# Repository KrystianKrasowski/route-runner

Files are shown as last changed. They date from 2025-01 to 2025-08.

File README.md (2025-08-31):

# Route Runner

## Table of contents

- [Overview](#overview)
- [Usage](#usage)
    - [Command referene](#command-reference)
    - [Dualshock 2 command mapping](#command---dualshock2-mapping)
    - [Modes reference](#modes-reference)
    - [LED modes mapping](#modes---led-indicator-mapping)
- [Hardware](#hardware)
    - [Power supply](#power-supply)
    - [GPIO usage summary](#gpio-usage-summary)
    - [Other peripherals usage summary](#other-peripheral-usage-summary)
    - [Electrical schematics](#electrical-schematics)
- [Software](#software)
    - [Application architecture](#application-architecture)
- [Development](#development)
- [Future work](#future-work)
- [Decision log](#decision-log)

## Overview

[YouTube video](https://youtu.be/DjguqcQfWMA)

Route runner is a name of the line following robot project. It is built using the following components:
* STM32 NUCLEO-F303 board as a microcontroller
* 2 DC motors driven by simple L293D driver
* Pololu's QTR-HD-06A line sensor
* Dualshock2 remote control
* 1 mode indicator LED
* Two LM2596 step-down voltage converters with the following settings:
    * 7V for the motors
    * 5V for the MCU and L293D logic

For the power details visit the [Power supply](#power-supply) section

## Usage
* Turn on the device using ON/OFF switch. Mode indicator displays MANUAL CONTROL mode.
* Place the vehicle or simply run it on the black line. Mode indicator displays DETECTED state. 
* Start line following by issuing FOLLOW command. Mode indicator displays TRACKING state.

### Command reference
* FORWARD - move forward
* BACKWARD - move backward
* RIGHT - turn right
* LEFT - turn left
* FOLLOW - start tracking the route
* BREAK - stop stracking
* PID Tune, Kp up/down - increase/decrease propotional factor by 10
* PID Tune, Ki up/down - increase/decrease integral factor by 1
* PID Tune, Kd up/down - increase/decrease derivative factor by 100

### Command - dualshock2 mapping
* FORWARD - R2
* BACKWARD - L2
* RIGHT - R2 or L2 + RIGHT
* LEFT - R2 or L2 + LEFT
* FOLLOW - START
* BREAK - CROSS
* PID Tune, Kp up - SQUARE + R1
* PID Tune, Kp down - SQUARE + L1
* PID Tune, Ki up - TRIANGLE + R1
* PID Tune, Ki down - TRIANGLE + L1
* PID Tune, Kd up - CIRCLE + R1
* PID Tune, Kd down - CIRCLE + L1

### Modes reference
* MANUAL - vehicle can be manually controlled
* DETECTED - vehicle sees the route beneath
* TRACKING - either FOLLOWING or RECOVERING
* FOLLOWING - vehicle sees and follows the route
* RECOVERING - vehicle does not see but still tries to get back on the route

> Note that the RECOVERING mode lasts only for 500ms unless route runner gets back on the route. After that time the vehicle will stop tracking.

### Modes - LED indicator mapping
* MANUAL - 1 short blink per second
* DETECTED - 2 short blinks per second
* TRACKING - 4 short blinks per second
* STACK OVERFLOW (FreeRTOS) 1 short blink, 1 long blink

> Short blink is a sequence `on -> off` with 250ms duration

> Long blink is a sequence `on -> off` with 500ms duration

## Hardware
* The line sensor is positioned at 4mm above the surface and the calibration is hardcoded.

### Power supply
The device is powered by two 18650 Li-ion 2500mAh 20A baterries of total voltage equal to 7.4V (3.7V each). The power buses are distributed as follows:
* 7V power bus provided by one of the LM2596 voltage converter. Used by L293D for DC motor inputs. Note that due to quite high voltage drops on L293D the effective voltage for DC motors whould oscilate around ~5V. This is not impressive and is the area to improve in the further project iterations.
* 5V power bus provided by the second LM2596 voltage converter. Used by L293D logic and the MCU
* 3.3V power bus provided by MCU. Used by the Dualshock2 receiver and state indicator
* 3.3V analog power bus provided by MCU. Used by line sensor
* Common GND bus for all components

### GPIO usage summary
* Motion:
    * **PB0** (D3) - PWM (tim3, ch3) for left motor
    * PB6 (D5) - A1 for right motor
    * PB7 (D4) - A2 for right motor
    * **PB1** (D6) - PWM (tim3, ch4) for right motor
    * PA10 (D0) - A2 for left motor
    * PA12 (D2) - A1 for left motor
* Remote control:
    * **PB5** (D11) - MOSI
    * **PB4** (D12) - MISO
    * **PB3** (D13) - SCK
    * PF0 (D7) - CS
* Line sensing:
    * *PA1* (A1) - channel 1
    * *PA3* (A2) - channel 2
    * *PA4* (A3) - channel 3
    * *PA5* (A4) - channel 4
    * *PA6* (A5) - channel 5
    * *PA7* (A6) - channel 6
* Status indicator
    * **PA8** (D9)
* USART
    * *PA15* - USART Rx
    * *PA2* - USART Tx

### Other peripheral usage summary
* TIM2 - timer for (dualshock2) MANUAL CONTROL communication trigger
* TIM3 channel 4 - timer for PWM signal for left motor (PB1)
* TIM3 channel 3 - timer for PWM signal for right motor (PB0)
* TIM6 - timer trigger for ADC conversion by TRGO, every 1ms
* TIM7 - timer for toggle sequence for blinking LED status indicator
* TIM15 - off route guard
* ADC12 in dual mode with DMA controller for conversions readings
* SPI1 bus - communication with Dualshock2 controller (via DMA)
* USART2 - serial communication with PC

Pins in **bold** are unchangeable. *Italic* pin change may implicate other changes.

### Electrical schematics
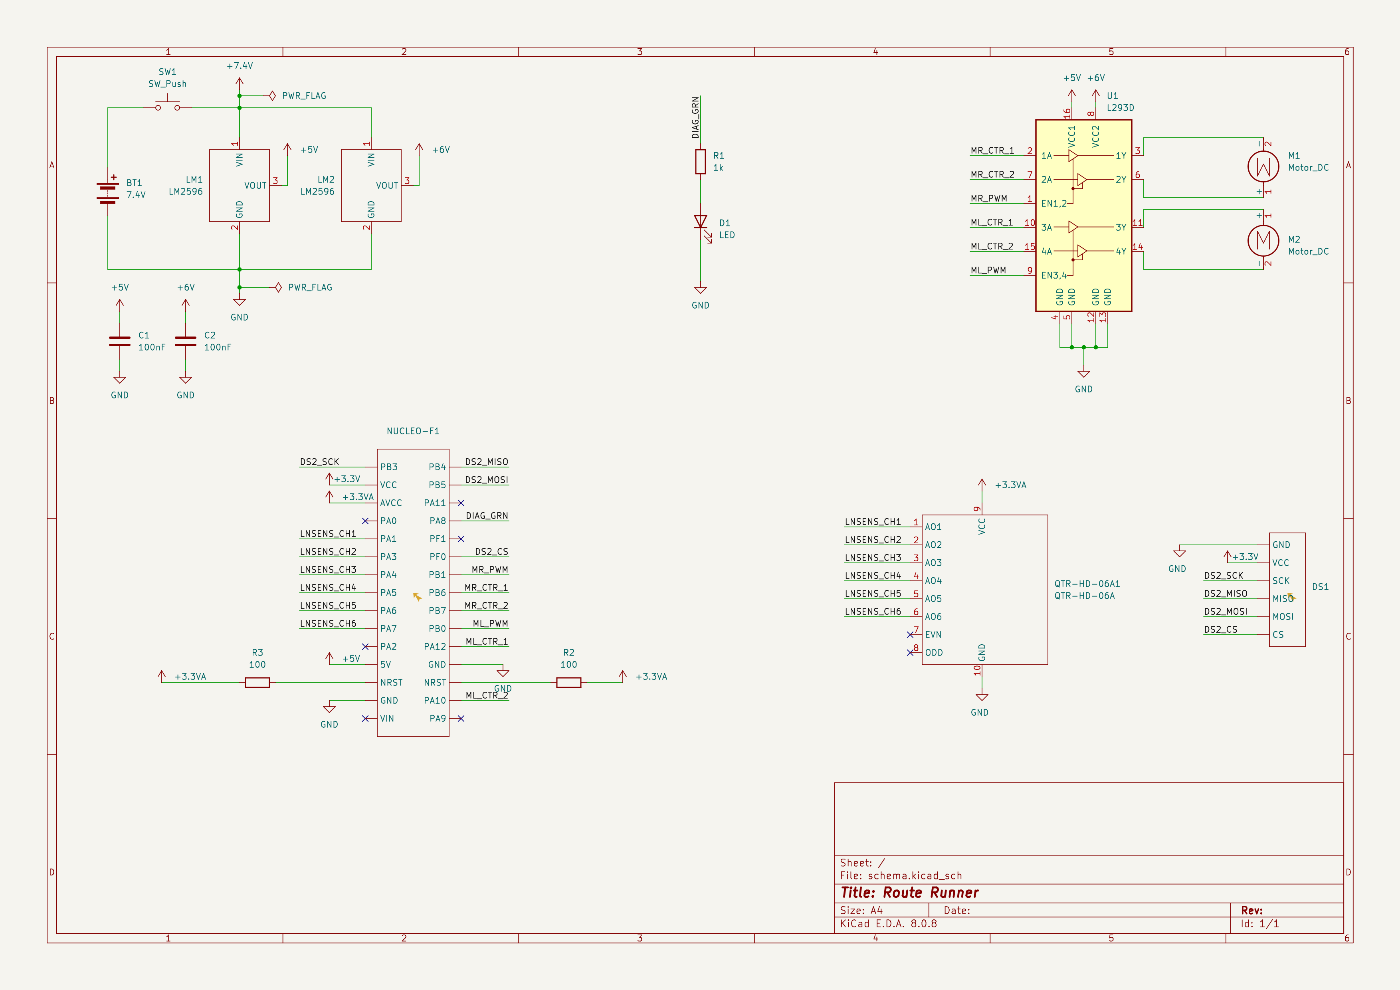
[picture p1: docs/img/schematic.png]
schematic


## Software

### Application architecture

Software architecture is inspired by the hexagonal (ports and adapters) pattern. The main goal of this approach was to be abe to embed the domain into any other MCU platform, wherher to use RTOS or bare metal, with or without STM32 HAL, etc. Any infrastructure change must not imply the domain logic changes.

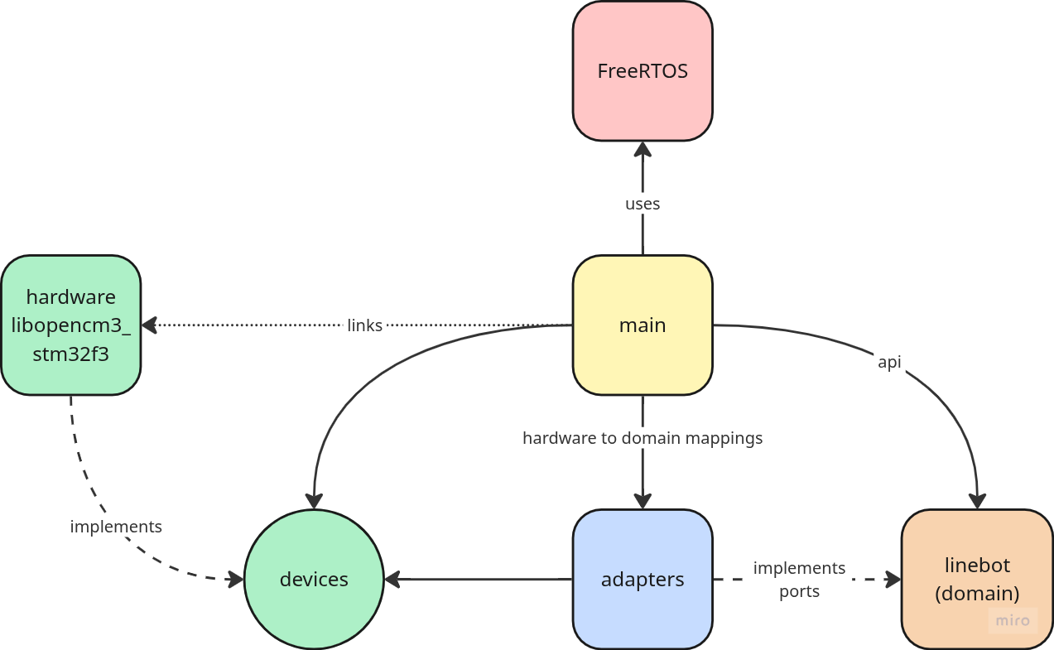
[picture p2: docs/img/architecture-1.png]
lib-dependency


## Development

Requirements:
* arm-none-eabi toolchain
* cmake

```bash
# build for flash
cmake --preset <release | debug>
cmake --build --preset <release | debug>

# flash
cmake --build --preset <release | debug> --target flash

# build for test
cmake --preset test
cmake --build --preset test
ctest --preset test
```

### Vim + LSP (clangd) setup

In order to work with vim+lsp driven by clangd keep in mind that the clangd must be run with `--query-driver` argument.
Here is an example of clangd lsp configuration via the vim-lsp-settings plugin

```
// PROJECT_ROOT/.vim-lsp-settings/settings.json
{
    "clangd": {
        "args": ["--query-driver=/usr/bin/arm-none-eabi-*"]
    }
}
```

## Future work

* Custom PCB design
    * Learning about bootloader
* Add display screen
    * Display battery discharge
    * Display PID parameters
    * Dispaly current mode
* Add some non-volatile memory for diagnostics storage

## Decision log
* [Application architecture pt. 1](./docs/decision-log/2025-01-11--app-architecture-pt1.md)
* [Application architecture pt. 2](./docs/decision-log/2025-02-02--app-architecture-pt2.md)
* [Duty cycle characteristic](./docs/decision-log/2025-03-24--duty-cycle-characteristic.md)
* [Opaque pointer/handle pattern](./docs/decision-log/2025-04-12--opaque.md)
* [Single function return](./docs/decision-log/2025-04-14--single-function-return.md)
* [Message queue](./docs/decision-log/2025-04-19--message-queue.md)
* [API command reentrancy](./docs/decision-log/2025-08-06--api-command-reentrancy.md)
* [Objects creation approach](./docs/decision-log/2025-08-30--objects-creation-approach.md)

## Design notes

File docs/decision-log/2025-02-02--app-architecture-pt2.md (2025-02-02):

# Application architecture

What application architecture to choose from:
* Layer
* Hexagonal

## Layer

Pros:
* Simple, strightforward
* Lighter binary

Cons:
* Not modular
* Component change implicates logic code refactor

## Hexagonal

Pros:
* Modular, extensible
* Scalable
* Unit test friendly

Cons:
* More complex
* Larger binary, maybe more RAM required

## Decision
Hexagonal. 

### Explanation
Unit tests are important to me as well as application to be extensible and scalable without a need to refactor logic. 

Examlpe 1. 
I can replace a motion adapter to the one that only displays some output to the serial console, just by editing a CMakeLists file in adapters package, without **any need to modify the code**.

Example 2.
I can develop an infrared pilot driver to remote control the device and switch between the controllers between IR and dualshock2, again, without any current code modification.

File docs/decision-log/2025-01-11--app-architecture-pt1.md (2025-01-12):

# Application architecture

What application architecture to choose from:
* RTOS
* Superloop

## Superloop

Pros:
* Simple, verbose and easy to start with
* Can introduce some of the architecture patterns like sequencer, finite state machine or serial task execution
* No/limited concurrency

Cons:
* No real time execution - for example when PID controller starts its computarion and the stop command appears, the PID algorithm will end its work first before stop command would execute
* Probably not industry way to go

## RTOS

Pros:
* Professional approach
* Industry standard
* Real time behaviour - for example stop command could suspend PID task execution

Cons:
* Steep learning curve
* Complex integration with non-HAL approach (or maybe not?)
* Concurrency

## Decision
To kickstart the project the **superloop** with **task sequencer** approach would be applied, along with custom, simple **messaging queue**

* It will allow smooth transition to RTOS
* The complexity at the start of the project will be decreased and the work can focus on PID control, accuracy of the device, etc
* Device functionality will not be as complex at first, that late response to STOP command would not be an issue.

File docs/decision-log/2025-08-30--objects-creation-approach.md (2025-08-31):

# How to create objects in embedded C++

## Subject
Should objects be created by Meyers' singleton or exposed by extern global?

## Big picture
* From the beginning of C++ refactor I took Meyers' singleton appraoch:
    * None of the objects in the application is created dynamically
    * All of the objects live as long as application itself
    * Almost all of the objects are single instance.

### Pros
* The same contract for all object creation, while at the same time the creation logic may differ. 
For example, the `L293` object that represents motor driver channel is on of the cases, when there are more than one instance.
The ETL object pool is used for such cases, but this solution isn't constrained to it. 
It can perform creation by local `static`, object pool, memory arena, freerfos heap, etc. At the same time only the static `of` method is exposed.

### Cons
* Constructor duplication - not as much a problem, but some inconveniance
* Threadsafe static - adds 4 bytes for each object despite the `-fno-threadsafe-statics` compiler flag
* Instatiation in main function prolongs initialization time - not noticable

## Alternative - extern global
* Objects can be statically created as their number and dependencies are known up-front

### Pros
* Less indirection
* Less memory usage

### Cons
* More boilerplate for initialization
* All application module would need to be refactored
* Extern mutable global is exposed - not huge issue - in the matter of fact the same applies with Meyers' singleton approach. 
It is visible only for modules that need this.
* Opens the door to manipulate the peripherals before initialization (for example logic in constructor - yes, bad practice, but nothing prevents from that besides common sense)

## Decision
Device tree is refactored to exposed global `g_device_tree`. Application sticks to Meyers' singleton

## Reasoning
* Refactoring devices layer is easy, saves noticable amount of memory usage, makes code much cleaner.
About peripherals manipulation in constructor - I believe in my common sense. And seriously - this is one person project for learning. Even if this is a mistake - good.
* Changing the whole application module would take quite amount of effort and time.
Since this is a place where freeRTOS API is called it is safer to call it at runtime.
Meyers' singleton forces lazy initialization which fits this requirement perfectly.
On top of that, with freeRTOS tasks, event groups, mutexes wrappers there is a bit of creation logic which currently used factory object is natural place to handle it.

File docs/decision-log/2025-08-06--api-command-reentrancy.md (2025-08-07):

# API Query/Command dispatcher reentrancy

## Subject
After splitting tasks into dispatcher and commands via event groups, the reentrancy problem occured.
API does not prevent itself from multiple calls of action methods, i. e. `apply_maneuver_by_remote`, `switch_mode_by_remotq`, etc.

Should I implement some locking mechanism?

## Big picture
* Expose only those methods from API: `query(remote_control)`, `query(line_position)`, `dispatch(action)`.
* The `query(...)` methods set action bits internally
* The `dispatch(...)` methods check bits and if set, clear and deletgate flow to private API method

### Pros
* API client uses only the product of the query outcome

### Cons
* Too much verbosity
* Overcomplication
* Reentrancy is not achived anyway - there still might be the case where two tasks race in the bit check condition.
Both might receive `true` from checking, therefore both might perform same action.

## Decision
Keep `query` method, keep action methods public as well.

## Reasoning
* **Overengineering**. This project is overengineered already :D (for learning purposes, of course).
* No profit, more stack call.
* `apply_maneuver_by_remote` isn't pure function - it depends on the `store_` state, yet it provides the same maneuver for the same store's state.
Reentrace of this method may only cause unnecesarry hardware updates, which should be delt anyway on the STM32 side
* `switch_mode_by_remote` method isn't pure function as well, yet it is idempotent, therefore it is safe to call mutliple times as well
* `tune_pid` method is the one to be careful about. Here it will be the caller responsibility not to call it more than once per query.
* If I ever wanted to synchronize, lock, wrap this in critical section, I'd prefer it to be the application layer responsibility,
as it provides FreeRTOS API that is well design for that cases: mutexes, semaphores, critical sections, etc.
* The last, but not least, as always - **YAGNI**

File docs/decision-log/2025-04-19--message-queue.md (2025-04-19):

# Message queue

## Subject
Is message queue for communication between the application layer and infrastructure layer good solution?

### Pros
* Good decoupling. Drivers does not know anything about applications and vice versa
* Backlog - from the mq perspective this is good and expected

### Cons
* May be huge memory requirement
* Backlog - from the line follower perspective we actually want to get rid of stale data
* Additional layer in application architecture

## Decision
No message queue is needed. The application task will read the data from drivers by adapters.

## Reasoning
* **YAGNI.** Although it gives good decoupling mechanism between the application and drivers layers, actually we do not need that. Application is an orchiestrator thus it should see every layer (or interface to it)
* **Huge memory usage.** Current implementation of mq has nice generic messages with byte-array payload. But this comes with a cost. Since we operate in embedded environment we want to use static arrays. And the payload needs to use as little memory as the biggest possible payload. Let's take a line sensor data. Now, the sensor itself averages the data in ISR which is not a good idea (ISR should be small and quick). That means that after refactor the sensor would put and array of **40 16bit integers**, meaning 80 bytes of memory. Plus `memcpy` to message payload, plus `memcpy` from message payload, plus conversion to `linebot_coords_t`. Morover, we have 3 mq topisc with 5 messages capacity. That gives us 3 * 5 * 80 **1,2kB just for message queue**. And thats insane, due to the fact that this solves a problems that we don't actually have. See below.
* **Backlog.** Line following robot should not handle the backlog for applying the motion. It should use only fresh data. As for now the ADC conversion is taking place once/1ms, thus the main loop has 1ms to perform: message conversion, mode update, PID computation, drive DC motors. 1ms is more than enough for this operations (**NEED BENCHMARK!**). It will never come to put more than one message on the queue topic. And if for some reason it did, the robot should not handle previous line coordinates as it is in constant motion and line position is changing dynamically. We actually want to drop stale data.
* **KISS.** The drivers will provide a function to get the newes data (some double buffering with bool flag). The function would return by out argument the value and return code to indicate that data is fresh or stale. The function's clinet - by proxy the application - will then decide to perform its task or not. The adapter proxy would perform averaging (line sensor case), etc and return the domain type directly. No `memcpy`s, no messages, not mq topics.

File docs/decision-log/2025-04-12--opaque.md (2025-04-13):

# Opaque handle

## Subject
Whether to use and opaque pointer (handle) pattern for the linebot domain module.

## Pros:
* Very nice nice module encapsulation
* Internals changes might not necessarly break the contract with clients
* Along with strong unit tests base the refactoring is nothing but joy

## Cons:
* Since dynamic memory allocation needs to be avoided, there is a need to implement fixed size object pools as well
* Because of above the memory isn't actually saved, since there will be no multiple objects in the pools:
    * context - 1 instance
    * position - 1 instance
    * motion - 1 instance
    * coords - 2 instances
* Need for NULL-check API public functions

## Decision: 
Opaque handle pattern will be used in linebot domain module.

## Reasoning:
* Pseudo-generic object pools implementation is great learning experiance and et’s not forget that this project is primarily focused on learning. Moreover this kind of patters along with memory arenas are common in embedded world.
* Number of object instances argument is actually a good one. I came across many suggestions that this is the case when opaque pattern may not be used. On the other hand, at this moment **I value encapsulation more** and accept this tradeoff.
* NULL check will be performed at the public API functions. It is still a good practice to check the validity of input arguments from the clinet-side, null check is actually part of the validation. The public function implementation can validate the input and pass the flow to some extracted module internal functions, which actually nicely separates the responsibilities of module parts. Internal module functions may assume valid handles to avoid redundant checks in performance-sensitive paths.

## Alternatives
* **Singleton pattern**. I definitely prefer single instance than singleton due to its ability to dependency inversion, thus much better unit test experiance. Also, singletons are actually static, encapsulated global variables. Without a good reason they should be avoided in my opinion. I don't state that they are evil, in fact, the message queue is singleton in current route-runner version. But it fits the pattern - it is accessed from different layers of application and need to be same instance always.
* **Structs defined in linebot module public headers**. Yes, there is a thin line here. Defining public structs and making them immutable does the job quite well, along with documentation warnings. However event the most strict documentation does not prevent the module user from misusing it. Although now there is no linebot module client other that the application itself, but adding some NULL checks at the top implementation level along with some object pools is not that much cost.

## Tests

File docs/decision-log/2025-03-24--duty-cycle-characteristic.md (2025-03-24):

# Duty cycle characteristic

What characteristic to choose for duty cycle per error relation:
* linear
* polynumeral
* linear with quadratic mix

# Description
The linear characteristic - `dc(e) = abs(-2 * abs(e) + 100)` - acts proportionally to the error, but there are areas on the track where vehicle reacts to very small curves.

The polynumeral characteristic whould give smooth transitions around 100 and 0 duty cycle values meaning, that the vehicle
would correct less near small errors. However finding the polynumeral (by Lagrange's interpolation) for given points is quite hard and results very small fractions making it difficult for processor to compute - or making the implementation more complex by using fixed point arithemtic.

The linear and quadratic mix smoothens ride only around of 100 duty cycle value. There is actually no need to smooth values around 0 because DC motor would stop spin around 10, thus it would smoothen itself. This is great compromise between two options above with the function result: 

```
dc(e) = abs(-2 * abs(e) + 100), for e < -50 and e > 50
dc(e) = -1/25 * e^2 + 100, for e >= 50 and e <= 50
```

# Decision
The duty cycle - error characteristic would be linear

# Explanation
There is literally no differance in vehicle performence between linear and mixed approach, so there is no need to make the implementation more complex. 

#Conclusion

Actually there should be no surprise. The PID regulator is applied, thus the real relation is between duty cycle and regulated error.

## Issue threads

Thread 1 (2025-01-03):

Basic circuit schematic

KrystianKrasowski, 2025-01-03:
AC:
* 7,4V power supply
* 6V voltage converter
* 3,3V voltage converter
* STM32L476RGTx Nucleo board
* L293 driver
* QTR-HD-06A line sensor
* IR sensor
* Status and mode LEDs

Closed 2025-01-04.

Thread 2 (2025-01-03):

Basic README.md file

KrystianKrasowski, 2025-01-03:
AC:
* Description of the project
* Usage
   * Turning on the device
   * IR pilot commands and device control
   * Status and mode LEDs meanings
* Technical information
   * Static line sensor callibration
* Development:
   * building and flashing the application commands

Closed 2025-01-04.

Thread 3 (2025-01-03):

Skeleton repository with a blinking LED application

KrystianKrasowski, 2025-01-03:
AC:
* Unit test ready application code with proper structure:
    * project_root
        * app - main entry point
        * doc - documentation
        * lib - 3rd party libraries with stm32 headers and startup code
        * src - application logic and drivers
        * test - unit tests for logic
* Blinking led application
* Some dummy logic with tests

Closed 2025-01-05.

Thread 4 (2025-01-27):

Project structure redesign

KrystianKrasowski, 2025-01-27:
AC:
* No `inc` folder - it is not a library but executable firmware
* All (reasonably) header files should be put along the implementation files
* App should follow the directory structure:
    * `/app` - main executable
    * `/config` - linker scripts
    * `/doc` - documentation, decision log, doxygen if used, etc
    * `/lib` - 3rd party libraries
    * `/src`
        * `/core` - core domain logic, decide how to name this package
        * `/utils` - application utils (ex. message queue)
        * `/drivers/peripherals` - target MCU peripheral drivers (with MCU suffix, ex. `pwm1_stm32f303xx.c`)
        * `/drivers/utils` - other components drivers, such as dualshock2 controller, decide how to name this package
    * `test` - unit tests

Closed 2025-01-27.

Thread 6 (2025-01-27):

Dualshock2 driver implementation

KrystianKrasowski, 2025-01-27:
AC:
* Implemented SPI driver, accepting whole command sequences, not single byte
* Display pressed button names in serial console, including button combinations

Closed 2025-02-02.

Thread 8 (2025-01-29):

Dummy task sequence

KrystianKrasowski, 2025-01-29:
AC:
* Serial console displays the output as described below

```
Command: STOP (5s delay)
Command: FORWARD (1s delay)
Command: FORWARD_RIGHT (1s delay)
Command: FORWARD_LEFT (3s delay)
Command: BACKWARD (1s delay)
Command: BACKWARD_RIGHT (1s delay)
Command: BACKWARD_LEFT (3s delay)
```

Implementation draft:
* Command should be triggered by timer interrupts
    * There should not be any task to run in a super loop that polls the actual command, thus the timer should be run in the init function
    * Each interrupt should enqueue some message about command change event
    * Try to use timer channel that is not associated with any PIN, as it will only be needed to trigger some event
* Command should be displayed by `printf` function using USART peripheral
    * Each command change event should be dequeued, translated and displayed
* Therefore there should be single tasks implemented:
    * display command change

Closed 2025-02-02.

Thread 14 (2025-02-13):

Review GPIO connection

KrystianKrasowski, 2025-02-13:
AC:
* An updated readme section of STM32F303 pin usage
* Distinguish unchangable pins from others (ex. two PWM lines cannot be used for anything else, analog lines as well, etc)

Closed 2025-02-13.

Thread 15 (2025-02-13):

State indicator LED implementation

KrystianKrasowski, 2025-02-13:
AC:
* Introduce a task for state indication
* Implement state indicator by blinking LED
* Invent LED behaviours, the example to start with is as follows:
    * 1 blnk per second - manual control
    * 4 blinks per second - line following
    * led on - line following finish
    * led toggling  - some error?

Note that the LED implementation is an implementation details. From the logic perspective there should be provided port for that. This will help for providing other state indicators such as LCD display in the future

Closed 2025-02-14.

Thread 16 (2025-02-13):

Create new electrical schema

KrystianKrasowski, 2025-02-13:
AC:
* replace nucleo board
* add analog sensor filtering
* change status indicator to one led only

Closed 2025-02-21.

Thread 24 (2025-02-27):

ADC driver implementation

KrystianKrasowski, 2025-02-27:
AC:
* Triggers every 1ms by some timer peripheral
* Works on minimum sampling time
* Loads conversions through DMA
* Provides ISR derived from DMA transfer complete with 30 conversions, 10 per channel
* README update with timer usage

Closed 2025-03-04.

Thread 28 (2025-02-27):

Change motion design

KrystianKrasowski, 2025-02-27:
AC:
* Use duty cycle percentage change instead of angle in motion object

Details:
Duty cycle delta should be computed proportionally to line drift, for example:
* 20% drift from the **left side of the line** - 20% decrease of the duty cycle on the **right motor**
* 35% drift from the **right side of the line** - 35% decrease of the duty cycle on the **left motor**

Closed 2025-03-05.

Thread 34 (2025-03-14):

Change error range

KrystianKrasowski, 2025-03-14:
AC:
* Come up with error range so that minimal change of ADC reading cause minimal change in error value

Closed 2025-03-16.

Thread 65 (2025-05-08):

Data oriented devices layer

KrystianKrasowski, 2025-05-08:
AC:
* Devices objects does not "own" data
    * dualshock SPI communication is based on DMA with explicit memory address specification
* Data store is encapsulated
* ISRs has no other logic than setting flags or other control flow alteration
    * TIM2 does not trigger SPI1 communication for dualshock, but only notify some main task to do so

Closed 2025-05-08.

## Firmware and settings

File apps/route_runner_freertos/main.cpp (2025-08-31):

#include "FreeRTOS.h"
#include "device/tree.hpp"
#include "isr_event_emitter_adapter.hpp"
#include "stack_overflow_handler.hpp"
#include "task.h"
#include "task_factory.hpp"

app::isr_event_emitter_adapter events;

int
main()
{
    device::g_device_tree.init(events);

    app::task_factory task_factory{device::g_device_tree, events};

#ifdef __DEBUG
    auto& manual_dispatch = task_factory.create_manual_control_dispatch_task();
    auto& manual_motion   = task_factory.create_manual_motion_task();
    auto& manual_mode     = task_factory.create_manual_mode_switch_task();
    auto& manual_pid_tune = task_factory.create_manual_pid_tune_task();
    auto& tracking_dispatch = task_factory.create_tracking_dispatch_task();
    auto& tracking_motion   = task_factory.create_tracking_motion_task();
    auto& tracking_mode     = task_factory.create_tracking_mode_switch_task();
    auto& route_guard       = task_factory.create_route_guard_toggle_task();
    auto& immediate_stop    = task_factory.create_immediate_stop_task();
    auto& shell_command     = task_factory.create_shell_command_task();
    auto& domain_dump       = task_factory.create_domain_dump_task();
    auto& shell_output      = task_factory.create_shell_output_task();
    auto& memory_usage      = task_factory.create_memory_usage_dump_task();

    memory_usage.monitor(manual_dispatch.describe());
    memory_usage.monitor(manual_motion.describe());
    memory_usage.monitor(manual_mode.describe());
    memory_usage.monitor(manual_pid_tune.describe());
    memory_usage.monitor(tracking_dispatch.describe());
    memory_usage.monitor(tracking_motion.describe());
    memory_usage.monitor(tracking_mode.describe());
    memory_usage.monitor(route_guard.describe());
    memory_usage.monitor(immediate_stop.describe());
    memory_usage.monitor(shell_command.describe());
    memory_usage.monitor(domain_dump.describe());
    memory_usage.monitor(shell_output.describe());
    memory_usage.monitor(memory_usage.describe());
#else
    (void)task_factory.create_manual_control_dispatch_task();
    (void)task_factory.create_manual_motion_task();
    (void)task_factory.create_manual_mode_switch_task();
    (void)task_factory.create_manual_pid_tune_task();
    (void)task_factory.create_tracking_dispatch_task();
    (void)task_factory.create_tracking_motion_task();
    (void)task_factory.create_tracking_mode_switch_task();
    (void)task_factory.create_route_guard_toggle_task();
    (void)task_factory.create_immediate_stop_task();
#endif

    (void)app::stack_overflow_handler::hook(
        device::g_device_tree.blink_,
        device::g_device_tree.motor_left_,
        device::g_device_tree.motor_right_
    );

    vTaskStartScheduler();

    // trap here in case of the scheduler error
    while (1)
    {
    }
}

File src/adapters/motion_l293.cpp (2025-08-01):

#include "adapter/motion_l293.hpp"
#include "device/l293.hpp"
#include "linebot/domain/maneuver.hpp"
#include <cstdint>
#include <etl/absolute.h>
#include <etl/map.h>
#include <etl/utility.h>

namespace adapter
{

constexpr int8_t  INVERT_TRESHOLD = 50;
constexpr uint8_t DUTY_CYCLE_MIN  = 0;
constexpr uint8_t DUTY_CYCLE_MAX  = 100;

constexpr uint8_t
duty_cycle(int8_t correction)
{
    // absolute value of linear function, V-shaped
    // y = | -2 * |x| + 100 |
    uint8_t duty_cycle = etl::absolute(-2 * etl::absolute(correction) + 100);

    // eliminate jitter on high values
    if (duty_cycle > 80)
    {
        duty_cycle = 100;
    }

    return duty_cycle;
}

motion_l293&
motion_l293::of(device::l293& motor_left, device::l293& motor_right)
{
    static motion_l293 motion_adapter{motor_left, motor_right};
    return motion_adapter;
}

void
motion_l293::apply(linebot::maneuver maneuver)
{
    if (last_maneuver_ == maneuver)
    {
        return;
    }

    motor_left_.disable();
    motor_right_.disable();

    auto rotation_left    = compute_left_rotation(maneuver);
    auto rotation_right   = compute_right_rotation(maneuver);
    auto duty_cycle_left  = compute_left_duty_cycle(maneuver);
    auto duty_cycle_right = compute_right_duty_cycle(maneuver);

    motor_left_.rotate(rotation_left);
    motor_right_.rotate(rotation_right);
    motor_left_.enable(duty_cycle_left);
    motor_right_.enable(duty_cycle_right);

    last_maneuver_ = maneuver;
}

device::l293::rotation
motion_l293::compute_left_rotation(linebot::maneuver maneuver)
{
    if (maneuver.is_forward() && maneuver.is_correction_below(-INVERT_TRESHOLD))
    {
        return device::l293::LEFT;
    }

    if (maneuver.is_backward()
        && maneuver.is_correction_below(-INVERT_TRESHOLD))
    {
        return device::l293::RIGHT;
    }

    if (maneuver.is_correction_at(-INVERT_TRESHOLD))
    {
        return device::l293::NONE;
    }

    return to_rotation(maneuver.get_direction());
}

device::l293::rotation
motion_l293::compute_right_rotation(linebot::maneuver maneuver)
{
    if (maneuver.is_forward() && maneuver.is_correction_above(INVERT_TRESHOLD))
    {
        return device::l293::LEFT;
    }

    if (maneuver.is_backward() && maneuver.is_correction_above(INVERT_TRESHOLD))
    {
        return device::l293::RIGHT;
    }

    if (maneuver.is_correction_at(INVERT_TRESHOLD))
    {
        return device::l293::NONE;
    }

    return to_rotation(maneuver.get_direction());
}

uint8_t
motion_l293::compute_left_duty_cycle(linebot::maneuver maneuver)
{
    if (linebot::maneuver::NONE == maneuver.get_direction())
    {
        return DUTY_CYCLE_MIN;
    }

    if (maneuver.is_correction_below(0))
    {
        return duty_cycle(maneuver.get_correction());
    }

    return DUTY_CYCLE_MAX;
}

uint8_t
motion_l293::compute_right_duty_cycle(linebot::maneuver maneuver)
{
    if (linebot::maneuver::NONE == maneuver.get_direction())
    {
        return DUTY_CYCLE_MIN;
    }

    if (maneuver.is_correction_above(0))
    {
        return duty_cycle(maneuver.get_correction());
    }

    return DUTY_CYCLE_MAX;
}

device::l293::rotation
motion_l293::to_rotation(linebot::maneuver::direction direction)
{
    switch (direction)
    {
    case linebot::maneuver::FORWARD:
        return device::l293::RIGHT;

    case linebot::maneuver::BACKWARD:
        return device::l293::LEFT;

    case linebot::maneuver::NONE:
    default:
        return device::l293::NONE;
    }
}

} // namespace adapter

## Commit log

2025-01-04 add electric schematic documentation
    [schema.kicad_pcb, schema.kicad_sch]
2025-01-04 fixed schematic
    [schema.kicad_sch]
2025-01-04 Add switch to the schematic. Add readme content
    [schema.kicad_sch]
2025-01-27 application structure redesign and stm32f303x8 target migration
2025-02-02 flatten drivers structure
2025-02-02 spi driver implementation
2025-02-05 move gpio handle to spi transfer logic
2025-02-14 tim1 driver and stack implementation
2025-02-16 switch to tim2 for triggering dualshock2 read - tim3 will be used for PWMs
2025-02-16 tim3 pwm implementation
2025-02-16 l293 driver implementation
2025-02-18 gpio l293 pin update along with documentation
2025-02-18 switch motion gracefully
2025-02-19 object oriented pwm
2025-02-20 change PWM channels assosiations
2025-02-21 Documentation update
    [schema.kicad_sch]
2025-02-25 add sysclock, set PLL as input, compute prescalers for timers
2025-02-25 adc standbox first version
2025-02-25 ADC dual mode
2025-03-01 systick delay, tim6 adc trigger, DMA transfer
2025-03-02 adc line sensing
2025-03-04 line sensor tests
2025-03-07 extract remote controll apply chain
2025-03-07 PID regulation - proportional factor
2025-03-07 adc interval increase, raw samples normalization, pid update only on new adc values
2025-03-10 full qtrhd06a line sensor service with dual adc
2025-03-10 add derivative and integral part for PID regulator
2025-03-11 extract PID motion regulation
2025-03-14 PID settings
2025-03-16 Remove integral factor from PID regulation
2025-03-16 PID regulation
2025-03-28 DMA configuration fix for release build
2025-03-28 reorganize adc driver code
2025-03-30 remove command apply chain for simplification
2025-03-30 remove mode apply chain and redundant functions
2025-03-30 extract PID regulator as strategy
2025-04-10 linebot SPI documentation
2025-04-15 Remove change mode by commands use case
2025-04-15 Rename stop use case
2025-04-17 describe ADC isr issue and simplify/optimize conversion
2025-04-19 test fixes; remove mq lib
    [dualshock2.c]
2025-04-21 new driver for l293
2025-04-22 gpio and timer abstractions
2025-04-23 add missing rcc initialization for timer; add pull down resistors for PWM OC pins
    [gpio.c]
2025-04-23 dualshock2 driver mock
2025-04-25 spi oo driver ;
2025-04-30 change device l293 setting rotation function
2025-04-30 renamed devices namespace
2025-05-02 add spi config
2025-05-04 add spi transmittion object and isr dispatcher
2025-05-04 adc driver implementation
2025-05-04 add qtrhd06a device driver
2025-05-05 added systick, fixed dma configuration, fixed qtrhd06a adapter readings
2025-05-06 add blink device
2025-05-06 add blink device mock
2025-05-06 encapsulate devices data store
2025-05-06 extract devices notifications from data store
2025-05-06 add tim15 for route guard device
2025-05-06 add timeout guard device
2025-05-07 static code analysis fixes
    [dualshock2.c]
2025-05-08 switch SPI communication control to DMA from interrupts
2025-05-08 pass notification id for QTR device as object dependency
2025-05-11 add pathbot tests for creating pid motion
2025-05-11 refactor PID motion creation
2025-05-13 change store data flow
2025-05-15 add handle commands use case
2025-05-15 add test cases for keeping current motion despite new commands
2025-05-16 add tracking use case
2025-05-16 add route guard timeout use case
2025-05-17 switch adapters to pathbot domain
2025-05-17 switch main to pathbot
2025-05-17 add coords normalization test case
2025-05-17 remove noop logic in handle commands use case
2025-05-17 remove logic from use case
2025-06-05 add serial_in device implementation
2025-06-07 encapsulate devices data store again
2025-06-09 add pid configuration dump on demand
2025-06-09 change dualshock dma mode to non-circular - smooth work in debug build
2025-06-09 move global dma channel 7 configuration to peripherals
2025-06-27 switch to static tasks - memory save
2025-06-27 rename devices notification port function
2025-06-27 adjust PID controller
2025-07-13 create toggle_sequence device
2025-07-13 dualshock2 device in cpp
2025-07-17 migrate to catch2 unit test framework
2025-07-18 linebot usecase - attempt mode switch
2025-07-18 linebot usecase - attempt mode switch - refactor
2025-07-22 add qtrhd06a cpp device and attempt maneuver by line position use case
2025-07-23 setup peripherals for ADC/QTRHD06A
2025-07-23 add qtrhd06 device to tree; introduce isr for qtrhd06a
2025-07-23 introduce qtrhd06a line sensor mapper
2025-07-24 introduce immediate stop task: timeout device, peripheral and isr handler setup, linebot logic, compose into task
2025-07-24 PID regulation on tracking mode
2025-07-28 directory names changes, last moder cmake dir structure touches
    [schema.kicad_pcb, schema.kicad_sch]
2025-07-28 Optimize memory footprint by unordered_map and float to int in printer
2025-07-29 change floats to fixed point integers in PID regulator
2025-07-30 add PID tuning commands mappings
2025-07-30 extract pid control from motion control
2025-08-01 PID tunning feature
2025-08-01 move jitter filter to motion adapter - it is duty cycle related, not pid steering value
    [motion_l293.cpp]
2025-08-02 Remove TODO for interrupt handlers registration
2025-08-06 add motor disable to stack overflow hook
2025-08-07 fix dma channel assignments for dualshock2
2025-08-23 Remove static creational method of the devices object, expose device tree as global
2025-09-23 constant device tree
